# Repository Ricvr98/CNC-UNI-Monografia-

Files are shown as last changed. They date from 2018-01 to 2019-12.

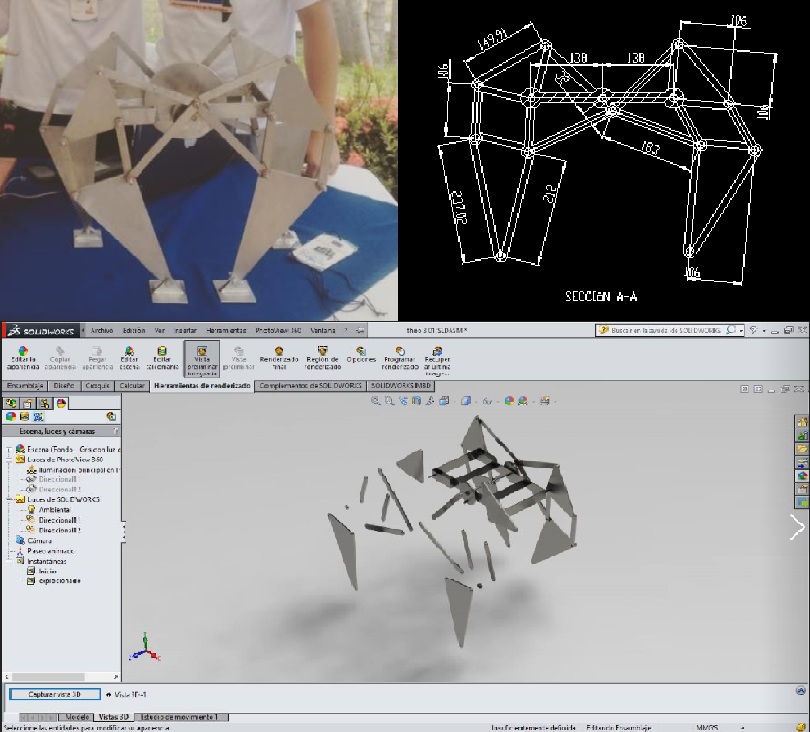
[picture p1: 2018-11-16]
conferencia/imagenes/diseño.jpg

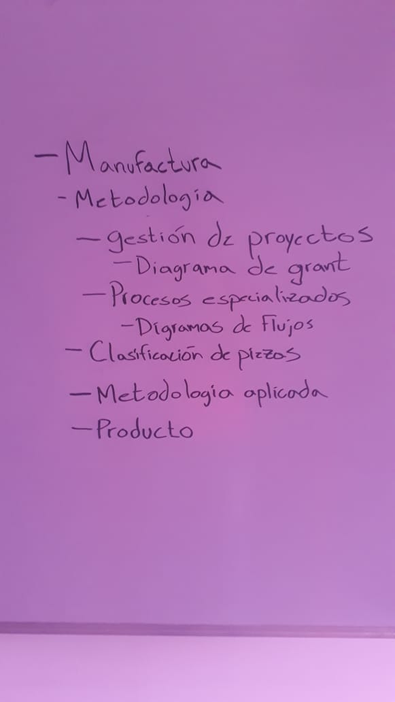
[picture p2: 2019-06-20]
bibliografia/Estructura manufactura.jpeg

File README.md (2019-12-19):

# CNC-UNI-Monografia-

-----------------CNC UNI 1.0------------------
===========================================================================================
Las máquinas de control numérico o CNC son el alma de la manufactura a gran escala
por lo tanto se ha decidido hacer un esfuerzo en entender la tecnología con el fin 
de facilitar la comprensión de cómo y cuándo se deben utilizar, además de que planteamos 
una metodología de diseño mecánico la cual hemos ido refinando a lo largo de los proyectos 
en los que hemos trabajado dejando en esta investigación nuestras conclusiones de cómo se 
debe elaborar un producto en este caso un CNC siendo esta monografía un arma de doble filo 
en donde se plantean los medios(Manufactura en máquinas CNC) para llevar a cabo el fin
(Producto) que se proponga. No está de más decir que se ha tratado de utilizar lo último 
en tendencias de diseño y que nuestro proyecto es open hardware el cual tiene como objetivo 
beneficiar a la mayor cantidad de gente directa o indirectamente.
___________________________________________________________________________________________
Importante
___________________________________________________________________________________________
Todo el software compartido en este proyecto es de terceros esto significa que ninguno de
estos programas fue desarrollodo por nosotros. Este proyecto mas bien plantea una recopilacion
de los programas que a nuestro criterio recomendamos.

La maquina necesita un conjunto de componentes electronicos y sus correspondientes software
para funcionar correctamente.
-------------------------------------------------------------------------------------------
Arduino MEGA 2560 + Ramps 1.4
-------------------------------------------------------------------------------------------
Este conjunto distribuye las instruciones de movimiento a los motores de los correspondientes
ejes.
El software relevante para el funcionamiento de este conjunto es:
	-IDE arduino
	-Librerias Marlin CNC y U8glib (https://github.com/MarlinFirmware/Marlin)
--------------------------------------------------------------------------------------------
Cad-cam 
--------------------------------------------------------------------------------------------
Con el objetivo de generar las geometrias de manera apropiada para esto proponemos el uso de 
Fusion 360 sin embargo se necesita el postprocesodor correcto para que la maquina entienda 
las instrucciones correctamente por lo tanto como postprocesador proponemos.
	-MPCnc Postprocessor (https://github.com/martindb/mpcnc_posts_processor)
---------------------------------------------------------------------------------------------
Interprete
---------------------------------------------------------------------------------------------
El trabajo del interprete es comunicar al microcontorlador de la maquina las instrucciones
previamente generadas en el programa CAM de una manera ordenada y legible para la maquina,
para esta tarea proponemos como interprete:
-Cncjs (https://github.com/cncjs/cncjs)

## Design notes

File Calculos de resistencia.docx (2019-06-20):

A continuación, se presentarán los cálculos de los ejes correspondientes para calcular la deflexión que se produce en la estructura metálica de la máquina. El método que se empleara para el cálculo de la deflexión máxima es el de área-momento.

Se hizo el análisis del cabezal del eje Z para el cual se hicieron algunas idealizaciones, tomando en cuenta que la fuerza que se aplica en el cabezal para transmitirla a las guías del eje Y es la componente de la fuerza de corte en el eje X, por lo tanto, se obtiene el siguiente análisis:

Material Aluminio

Perfil en L

E=69 GP_a

I_X =I_Y =1.44x10^5 mm^4

∑ F_X =0

∑ F_Y =0

∑ M_A =0

R_(Ax) +R_(Bx) -F_1 =0

R_(Ay) +R_(By) =0

(R_(Bx) *L_(AB) )+(F_1 *L_(AC) )=0

R_(Ax) =-R_(Bx) +F_1

R_(Ay) =-R_(By)

R_(Bx) =(F_1 *L_(AC))/(L_(AB))

R_(Bx) =(131.44N*157.3mm)/(60.3mm)

R_(Bx) =343.0529N

R_(Ax) =-342.8775N+131.44N

R_(Ax) =-211.6129N

Cálculo del área-momento

B=(M_B)/(EI)

B=(-12749.68N)/((69*10^3 N*mm^2 )(1.44*10^5 mm^4 ))

B=-1.2832*10^(-6) mm^(-1)

∆_c =|t_(C/A) |-∆^(´)

Por relación de triángulos semejantes se tiene que:

(∆^(´))/(L_(AC))=(t_(B/A))/(L_(AB))

∆^(´) =(t_(B/A) *L_(AC))/(L_(AB))

∆^(´) =(157.3mm)/(60.3mm)*t_(B/A)

∆^(´) =2.61*t_(B/A)

|t_(B/A) |=1/3L_(AB) *(1/2*M/(EI)*L_(AB) )

|t_(B/A) |=1/3(60.3mm)(1/2*M/(EI)*60.3mm)

|t_(B/A) |=605.0104 mm^2 *M/(EI)

|t_(C/A) |=L_(AB) *(1/2*M/(EI)*L_(AC) )

|t_(C/A) |=60.3mm*(1/2*M/(EI)*157.3mm)

|t_(C/A) |=4737.1563mm^2 *M/(EI)

∆_c =|t_(C/A) |-∆^(´)

∆_c =|t_(C/A) |-2.61*t_(B/A)

∆_c =4737.1563 mm^2 *M/(EI)-2.61*(605.0104 mm^2 *M/(EI))

∆_c =(4737.1563 mm^2 *1.2832*10^(-6) mm^(-1) )-2.61*(605.0104 mm^2 *1.2832*10^(-6) mm^(-1) )

∆_c =4.0524*10^(-3) mm

Los rodamientos del cabezal del eje Z están distribuidos de forma simétrica, por lo tanto, se tiene la deflexión máxima calculada para el cabezal es igual en ambos lados de los cojinetes. De esta manera se tiene que esta deflexión máxima es permisible a la hora de maquinar sobre aluminio.

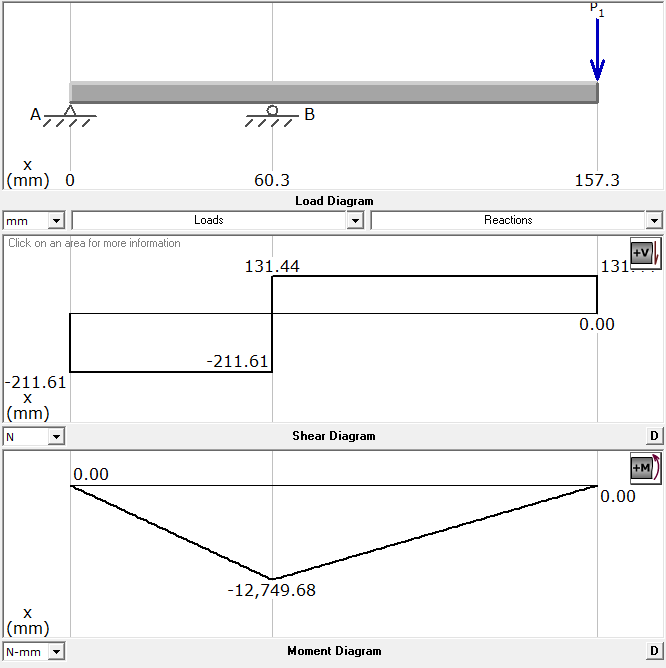
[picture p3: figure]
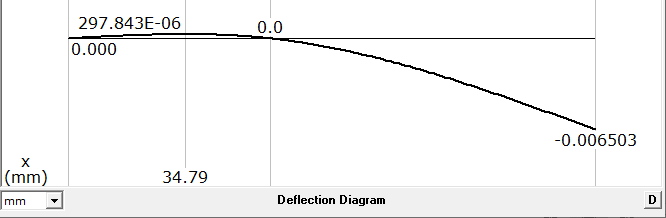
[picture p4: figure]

Guías lineales

Material: Aleación Cromo-Níquel

Perfil Circular

E=210 GP_a ≅210 (KN)/(mm^2)

I=1.02x10^3 mm^4

En el análisis de las fuerzas que actúan en las guías lineales se observa que esta doblemente empotrada y es de condición hiperestática. Se observo en el libro de resistencia de materiales 5ta edición de Robert L. Mott en el apéndice A-25 que la guía se comporta de la misma manera en que está representado ahí, por lo que se ocuparan las formulas ya planteadas solo cambiando el signo de la formula según el sentido de la fuerza.

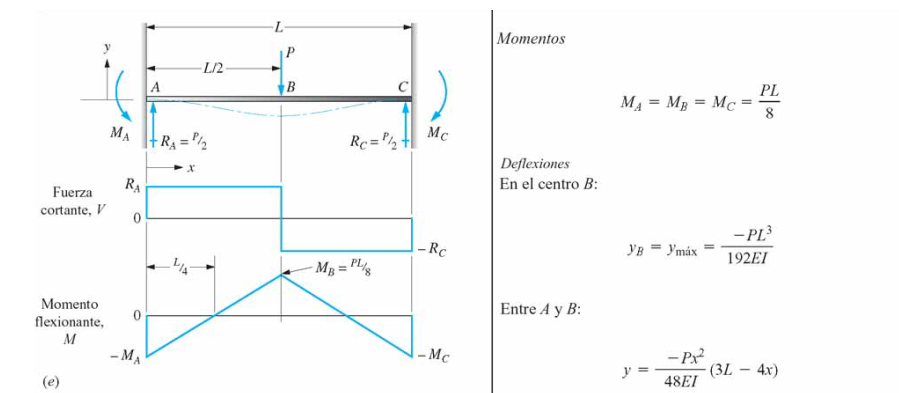
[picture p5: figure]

Para la Guía Lineal #1 la fuerza se comporta en el mismo sentido de la figura.

Las reacciones están de la siguiente manera:

R_A =R_B =(F_1)/2

R_A =(211.6129 N)/2

R_A =105.80645 N

Los momentos flexionantes son:

M_A =M_B =M_C =(F_1 L)/8

M_A =(211.80645 N*274 mm)/8

M_A =7247.7018 N*mm

La deflexión máxima en el punto B es:

y_B =y_(máx) =(F_1 *L_(AC)^3)/(192EI)

y_B =(211.80645N*(274mm)^3)/(192*(210*10^3 N/(mm^2))*(1.02*10^3 mm^4 ))

y_B =0.10581 mm

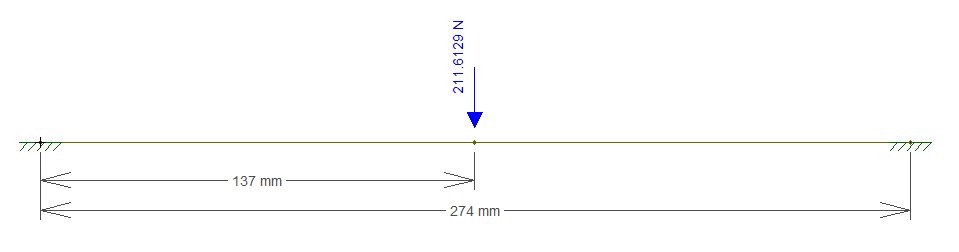
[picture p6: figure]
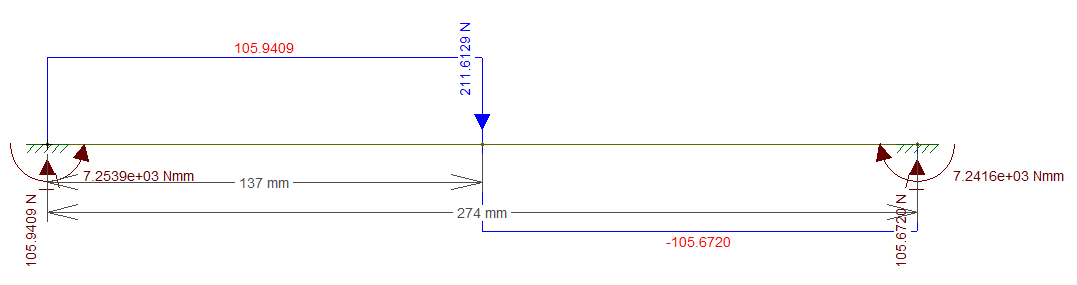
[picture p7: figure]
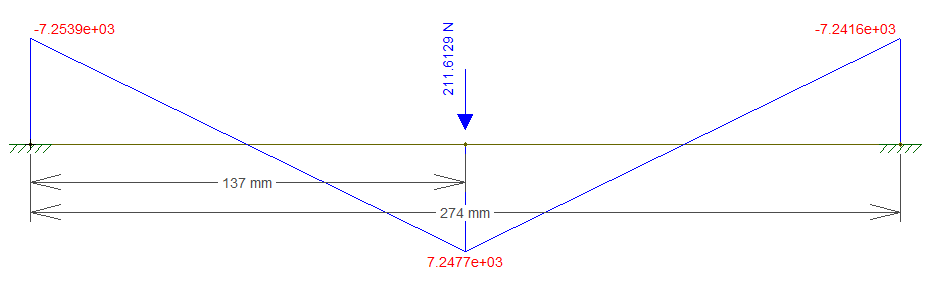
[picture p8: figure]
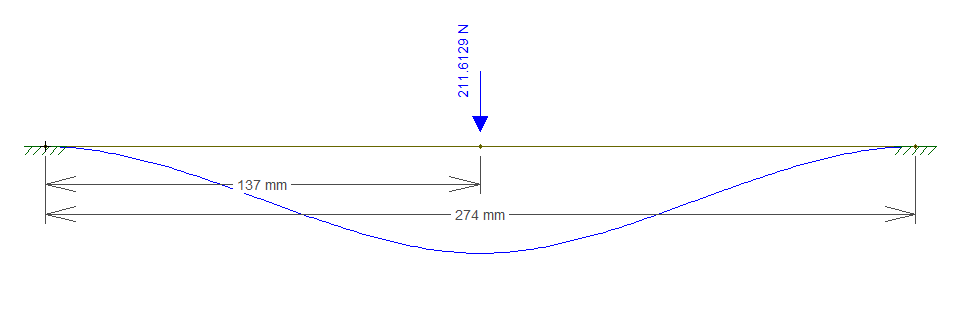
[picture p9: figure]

0.1058 mm

La guía lineal #2 se comporta de la misma manera solo que el sentido de la fuerza es en sentido contrario.

Las reacciones están de la siguiente manera:

R_A =R_B =(F_1)/2

R_A =(343.0529 N)/2

R_A =171.52645 N

Los momentos flexionantes son:

M_A =M_B =M_C =(F_1 L)/8

M_A =(343.0529 N*274 mm)/8

M_A =11749.56183 N*mm

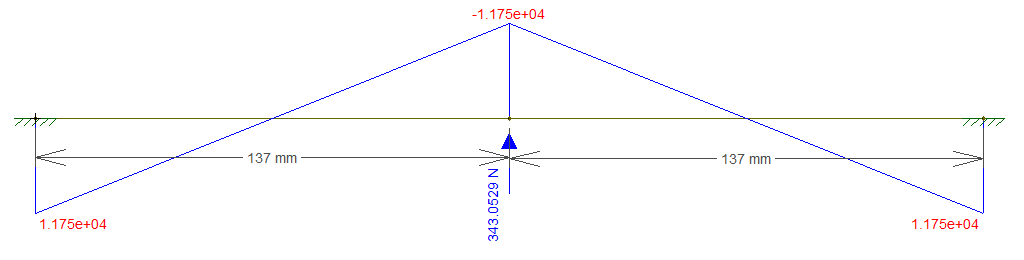
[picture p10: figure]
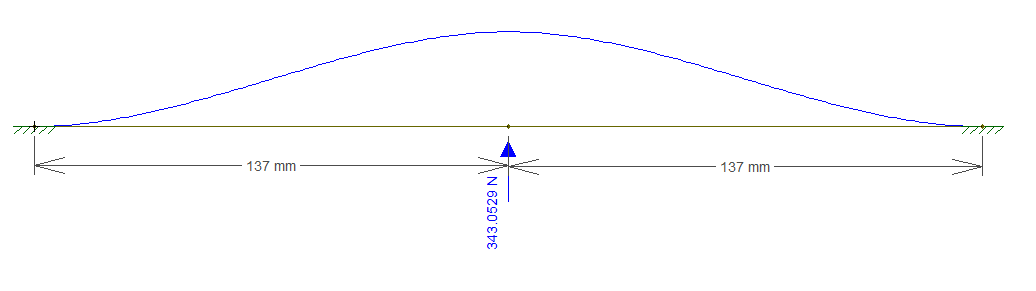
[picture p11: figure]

La deflexión máxima en el punto B es:

0.1716 mm

y_B =y_(máx) =(F_1 *L_(AC)^3)/(192EI)

y_B =(343.0529N*(274mm)^3)/(192*(210*10^3 N/(mm^2))*(1.02*10^3 mm^4 ))

y_B =0.1716 mm

Cálculo de resistencia de los parales de la estructura metálica

Material: Acero estructural

E=200 GP_a =200 (KN)/(mm^2)

∑ F_X =0

∑ F_z =0

∑ M_A =0

R_(Ax) -F_2 +F_1 =0

R_(Az) =0

M_A +M_B -M_C +(F_2 *L_(AB) )-(F_1 *L_(AC) )=0

R_(Ax) =F_2 -F_1

R_(Ax) =171.52645N-105.80645N

R_(Ax) =65.72N

M_A =-M_B +M_C +(F_2 *L_(AB) )-(F_1 *L_(AC) )

M_A =-11749.56183N*mm+7247.7418+(171.52645N*292.5mm)-(105.80645N*470mm)

M_A =-11749.56183N*mm+7247.7418+(50171.48663N*mm)-(49729.0315N*mm)

M_A =-4059.3649N*mm

Es un perfil rectangular hueco de 2”x1”x1/16” de medidas externas (50.8mm x 25.4mm x 1.5875mm)

Medidas internas 1.875”x0.875” (47.625mm x 22.225mm)

I=(b*h^3)/12-(b*h^3)/12

I=((25.4mm)*(50.8mm)^3)/12-((22.225mm)(47.625mm)^3)/12

I=277487.6171mm^4 -200062.407mm^4

I=77.43x10^3 mm^4

Cálculo del área-momento

A=(M_A)/(EI)

A=(4059.36491N*mm)/((2.00*10^5 N*mm^2 )(77.43*10^3 mm^4 ))

B=2.6*10^(-7) mm^(-1)

B=(M_B)/(EI)

B=(23282.46491N*mm)/((2.00*10^5 N*mm^2 )(77.43*10^3 mm^4 ))

B=1.5*10^(-6) mm^(-1)

B=(M_B)/(EI)

C=(11532.90308N*mm)/((2.00*10^5 N*mm^2 )(77.43*10^3 mm^4 ))

C=7.5*10^(-7) mm^(-1)

C=(M_A)/(EI)

C=(-7247.7418N*mm)/((2.00*10^5 N*mm^2 )(77.43*10^3 mm^4 ))

C=-4.7*10^(-7) mm^(-1)

∆_c =|t_(B/A) |+∆^(´)

Por relación de triángulos semejantes se tiene que:

(∆^(´))/(L_(AC))=(t_(B/A))/(L_(AB))

∆^(´) =(t_(B/A) *L_(AC))/(L_(AB))

∆^(´) =(470mm)/(292.5mm)*t_(B/A)

∆^(´) =1.61*t_(B/A)

|t_(B/A) |=1/3L_(AB) *(1/2*(M_1)/(EI)*L_(AB) )+1/2L_(AB) *((M_2)/(EI)*L_(AB) )

|t_(B/A) |=1/3(292.5mm)*(1/2*1.2*10^(-6) mm^(-1) *292.5mm)+1/2*292.5mm*(2.6*10^(-7) mm^(-1) *292.5mm)

|t_(B/A) |=0.02mm+0.01mm

|t_(B/A) |=0.03mm (Deflexión máxima en el punto B)

∆^(´) =1.61*t_(B/A)

∆^(´) =1.61*0.03

∆^(´) =0.05mm

∆_c =|t_(B/A) |+∆^(´)

∆_c =0.03mm+0.05mm

∆_c =0.08mm(Deflexión máxima en el punto C)

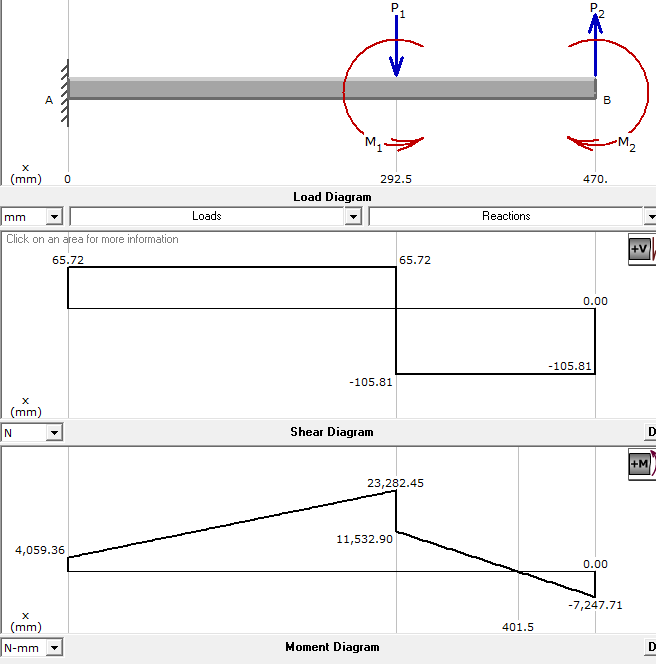
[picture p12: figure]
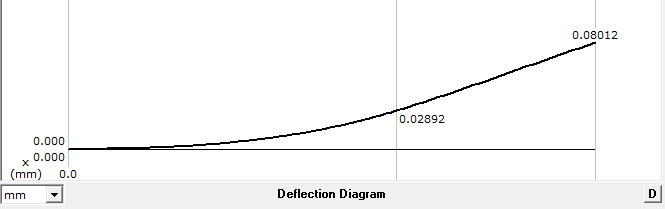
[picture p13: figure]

Los parales verticales de la estructura metálica tienen una deflexión máxima de 0.08 mm, por lo tanto, se concluye que la estructura metálica es lo suficientemente rígida para soportar el maquinado de materiales como el aluminio.

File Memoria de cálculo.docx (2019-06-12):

Memoria de cálculo.

Nota: se tomará el área como unidad correspondiendo a la unidad de medida de la fuerza de corte.

Fc1= 500 N/mm (fuerza de corte especifica por unidad de mm)

Ac = 1 mm (Área de Corte)

ae= 5mm (profundidad de corte radial)

Z’= 0.15 (factor de corrección)

Z= 4 (número de filos)

n= RPM (revoluciones por minuto)

Vf= 1000 mm/min (velocidad de avance)

f_z =(V_f)/(n*z) (avance por diente)

f_z =(1000 (mm)/(min))/((12000 rpm*4))

f_z =0.02083 (mm)/(rev)

h_m =(f_z *a_e *360)/(D*π*cos^(-1) [1-(2a_e)/D])

h_m =(0.02083(mm)/(rev)*5mm*360)/(9mm*π*cos^(-1) [1-(2*5mm)/(9mm)])

h_m =0.01376 mm

F_c^(,) =F_(C_1) *h_m ^(z^(,)) (fuerza de corte especifica)

F_c^(,) =500 N/(mm) *(0.01376mm)^0.15

F_c^(,) = 262.88 N/(mm^2)

F_c =F_c^(,) *A_c (Fuerza de corte)

F_c =262.88 N/(mm^2)*1 mm^2

F_c =262.88 N

# Tornillo de potencia del eje Z

-Z

Z

## Movimiento vertical

Fuerzas que actúan.

Fi= 4.90 kgf

Ff= 0.882 kgf

N= 4.90 kgf

µ=0.18

Fm= 262.88 N ≈ 26.7971 kgf

Velocidades de trabajo.

Vo= 0

V1= Vmáx

V2= Vmáx

V3= Vm

V4= Vm

V5= 0

V6= Vm

V7= Vm

V8= Vmáx

V9= Vmáx

V10= 0

Ff

Fuerzas que actúan en el tornillo dependiendo de las velocidades de trabajo.

Fi

Fa_1 =F_i -F_f ; Fa_1 =(4.9-0.882)kgf ; Fa_1 =4.018 kgf

Ff

Fa_2 =-F_f ; Fa_2 =-0.882 kgf

Ff

Fi

Fa_3 =F_i -F_f ; Fa_3 =(4.9-0.882)kgf ; Fa_3 =4.018 kgf

Fm

Fa_4 =F_f -F_m ; Fa_4 =(0.882-26.7971)kgf ; Fa_4 =-25.9151 kgf

Ff

Ff

Fa_5 =F_f ; Fa_5 =0.882 kgf

Ff

Fa_6 =-F_f ; Fa_6 =-0.882 kgf

Ff

Fa_7 =F_m -F_f ; Fa_7 =(26.7971-0.882)kgf ; Fa_7 =25.9151 kgf

Fm

Ff

Fi

Fa_8 =F_f -F_i ; Fa_8 =(0.882-4.9)kgf ; Fa_8 =-4.018

Ff

Fa_9 =F_f ; Fa_9 =0.882 kgf

Ff

Fi

Fa_10 =F_f -F_i ; Fa_10 =(0.882-4.9)kgf ; Fa_10 =-4.018 kgf

Torque requerido para subir una carga.

F= 4.9 kgf

f=0.18

φ= 14.5°

D= 7.9375 mm

P= 1.81356 mm (L)

Dr=5.4356 mm

Dp= 6.63956 mm

At= 28.6322008 plg²

As=280.257504 plg²

tanλ=L/(πD_p) (ángulo de avance)

tanλ=(1.81356mm)/(π*6.63956mm) ; λ=tan^(-1) ((1.81356mm)/(π*6.63956mm))

λ=4.9691°

Torque necesario para subir una carga.

T_u =(FD_p)/2[(cosϕtanλ+f)/(cosϕ-ftanλ)]

T_u =(4.90kgf*6.63956mm)/2[(cos(14.5)tan(4.9691)+0.18)/(cos(14.5)-0.18tan(4.9691))]

T_u =4.5116 kgf*mm

T_u =(4.5116 kgf*mm)*(1cm)/(10mm)*(9.81N)/(1kgf)

T_u =4.4259 N*cm

Torque requerido para bajar una carga.

T_d =(FD_p)/2[(f-cosϕtanλ)/(cosϕ+ftanλ)] Torque necesario para bajar una carga

T_d =(4.90kgf*6.63956mm)/2[(0.18-cos(14.5)tan(4.9691))/(cos(14.5)+0.18tan(4.9691))]

T_d =1.5844 kgf*mm

T_d =(1.5844 kgf*mm)*(1cm)/(10mm)*(9.81N)/(1kgf)

T_d =1.5543 N*cm

Tornillo de potencia del eje X

## Movimiento horizontal

X

-X

Fuerzas que actúan.

Fi= 7.02 kgf

Ff= 1.2636 kgf

N= 7.02 kgf

µ=0.18

Fm=262.88 N ≈ 26.7971 kgf

Velocidades de trabajo.

Vo= 0

V1= Vmáx

V2= Vmáx

V3= Vm

V4= Vm

V5= 0

V6= Vm

V7= Vm

V8= Vmáx

V9= Vmáx

V10= 0

Fi

-Ff

Fuerzas que actúan en el tornillo dependiendo de las velocidades de trabajo.

Fa_1 =F_i -F_f ; Fa_1 =(7.02-1.2636)kgf ; Fa_1 =5.7564 kgf

-Ff

Fi

-Ff

Fa_2 =-F_f ; Fa_2 =-1.2636 kgf

Fa_3 =F_i -F_f ; Fa_3 =(7.02-1.2636)kgf ; Fa_3 =5.7564 kgf

Fa_4 =F_f -F_m ; Fa_4 =(1.2636-26.7971)kgf ; Fa_4 =-25.5335 kgf

Ff

-Fm

Ff

Fa_5 =F_f ; Fa_5 =1.2636 kgf

-Ff

-Ff

Fa_6 =-F_f ; Fa_6 =-1.2636 kgf

Fm

Fa_7 =F_m -F_f ; Fa_7 =(26.7971-1.2636)kgf ; Fa_7 =25.5335 kgf

Fa_8 =F_f -F_i ; Fa_8 =(1.2636-7.02)kgf ; Fa_8 =-5.7564 kgf

Ff

-Fi

Ff

Fa_9 =F_f ; Fa_9 =1.2636 kgf

Ff

-Fi

Fa_10 =F_f -F_i ; Fa_10 =(1.2636-7.02)kgf ; Fa_10 =-5.7564 kgf

Torque necesario para subir una carga.

T_u =(FD_p)/2[(cosϕtanλ+f)/(cosϕ-ftanλ)]

T_u =(7.02kgf*6.63956mm)/2[(cos(14.5)tan(4.9691)+0.18)/(cos(14.5)-0.18tan(4.9691))]

T_u =6.4636 kgf*mm

T_u =(6.4636 kgf*mm)*(1cm)/(10mm)*(9.81N)/(1kgf)

T_u =6.3408 N*cm

Torque requerido para bajar una carga.

T_d =(FD_p)/2[(f-cosϕtanλ)/(cosϕ+ftanλ)] Torque necesario para bajar una carga

T_d =(7.02kgf*6.63956mm)/2[(0.18-cos(14.5)tan(4.9691))/(cos(14.5)+0.18tan(4.9691))]

T_d =2.2700 kgf*mm

T_d =(2.2700 kgf*mm)*(1cm)/(10mm)*(9.81N)/(1kgf)

T_d =2.2269 N*cm

# Tornillo de potencia del eje Y

## Movimiento horizontal

Y

-Y

Fuerzas que actúan.

Fi= 3.09 kgf

Ff= 0.5562 kgf

N= 3.09 kgf

µ=0.18

Fm=262.88 N ≈ 26.7971 kgf

Velocidades de trabajo.

Vo= 0

V1= Vmáx

V2= Vmáx

V3= Vm

V4= Vm

V5= 0

V6= Vm

V7= Vm

V8= Vmáx

V9= Vmáx

V10= 0

Fi

-Ff

Fuerzas que actúan en el tornillo dependiendo de las velocidades de trabajo.

Fa_1 =F_i -F_f ; Fa_1 =(3.09-0.5562)kgf ; Fa_1 =2.5338 kgf

-Ff

Fi

-Ff

Fa_2 =-F_f ; Fa_2 =-0.5562 kgf

Fa_3 =F_i -F_f ; Fa_3 =(3.09-0.5562)kgf ; Fa_3 =2.5338 kgf

Fa_4 =F_f -F_m ; Fa_4 =(0.5562-26.7971)kgf ; Fa_4 =-26.2409 kgf

Ff

-Fm

Ff

Fa_5 =F_f ; Fa_5 =0.5562 kgf

-Ff

-Ff

Fa_6 =-F_f ; Fa_6 =-0.5562 kgf

Fm

Fa_7 =F_m -F_f ; Fa_7 =(26.7971-0.5562)kgf ; Fa_7 =26.2409 kgf

Fa_8 =F_f -F_i ; Fa_8 =(0.5562-3.09)kgf ; Fa_8 =-2.5338 kgf

Ff

-Fi

Ff

Fa_9 =F_f ; Fa_9 =0.5562 kgf

Ff

-Fi

Fa_10 =F_f -F_i ; Fa_10 =(0.5562-3.09)kgf ; Fa_10 =-2.5338 kgf

Torque necesario para subir una carga.

T_u =(FD_p)/2[(cosϕtanλ+f)/(cosϕ-ftanλ)]

T_u =(3.09kgf*6.63956mm)/2[(cos(14.5)tan(4.9691)+0.18)/(cos(14.5)-0.18tan(4.9691))]

T_u =2.8451 kgf*mm

T_u =(2.8451 kgf*mm)*(1cm)/(10mm)*(9.81N)/(1kgf)

T_u =2.7910 N*cm

Torque requerido para bajar una carga.

T_d =(FD_p)/2[(f-cosϕtanλ)/(cosϕ+ftanλ)] Torque necesario para bajar una carga

T_d =(3.09kgf*6.63956mm)/2[(0.18-cos(14.5)tan(4.9691))/(cos(14.5)+0.18tan(4.9691))]

T_d =0.9992 kgf*mm

T_d =(0.9992 kgf*mm)*(1cm)/(10mm)*(9.81N)/(1kgf)

T_d =0.9802 N*cm

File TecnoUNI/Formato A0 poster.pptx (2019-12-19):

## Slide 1

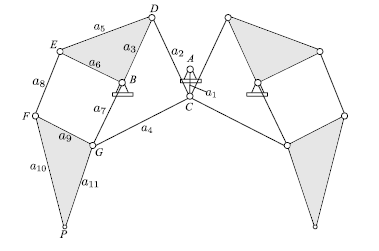
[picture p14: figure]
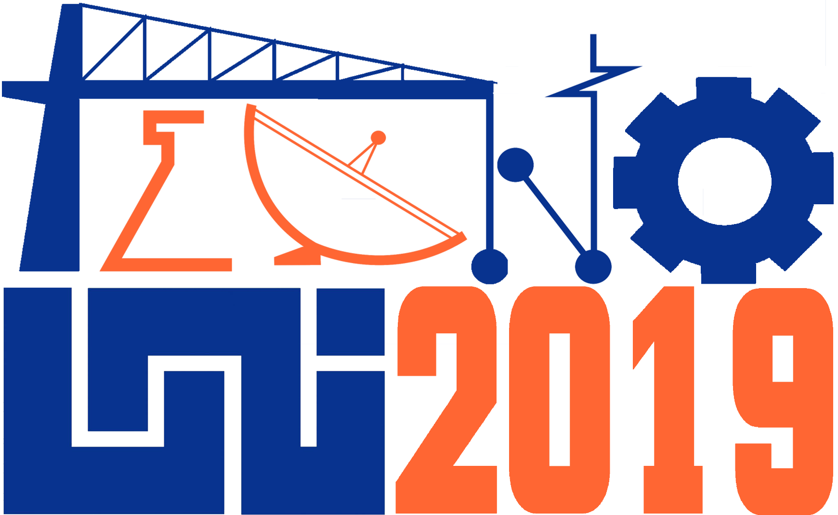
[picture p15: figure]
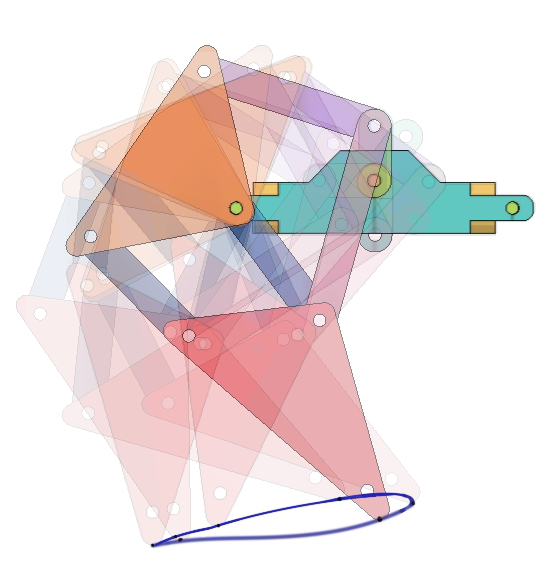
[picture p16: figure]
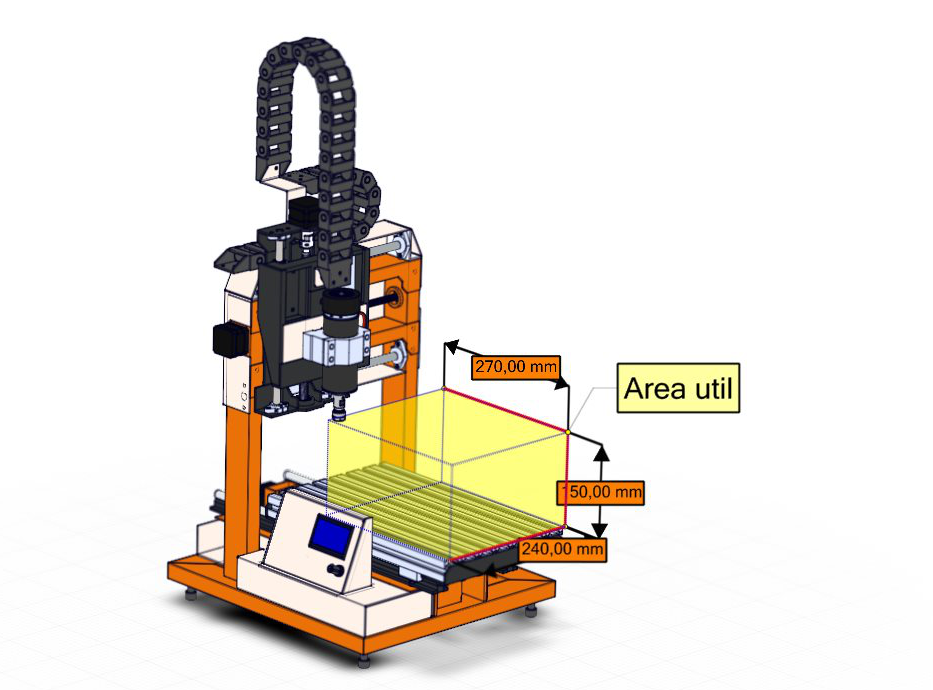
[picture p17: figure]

Manufactura en maquinaria CNC aplicada a
proyectos académicos y posibles usos en la
industria local

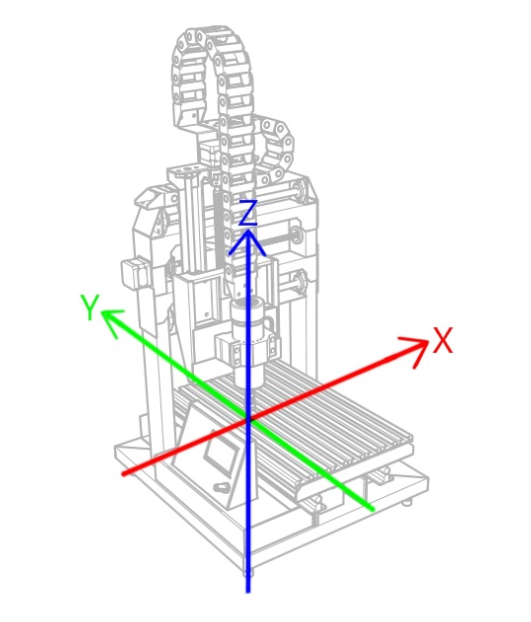
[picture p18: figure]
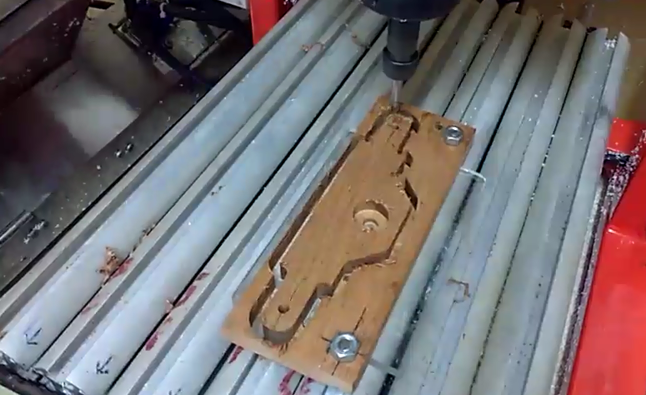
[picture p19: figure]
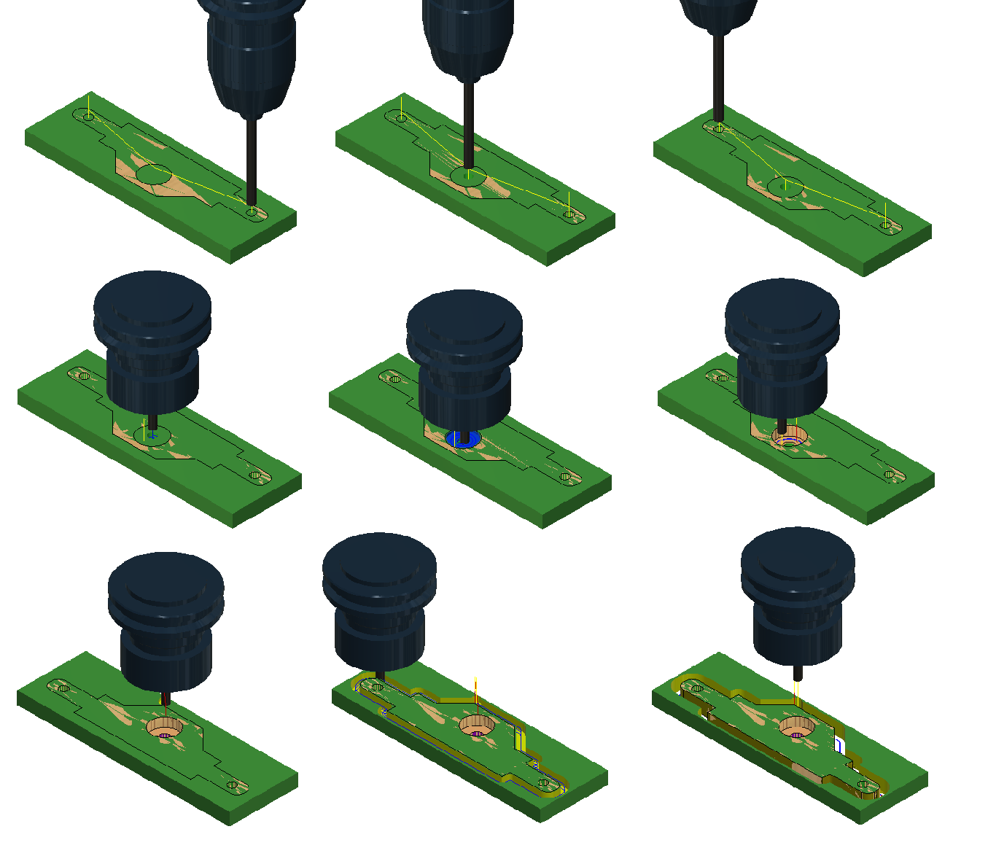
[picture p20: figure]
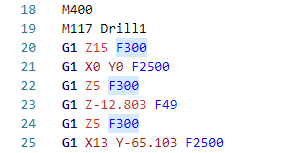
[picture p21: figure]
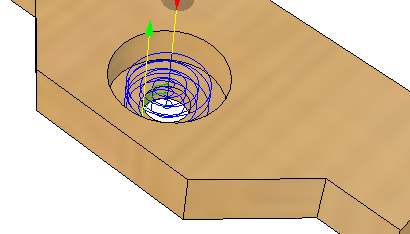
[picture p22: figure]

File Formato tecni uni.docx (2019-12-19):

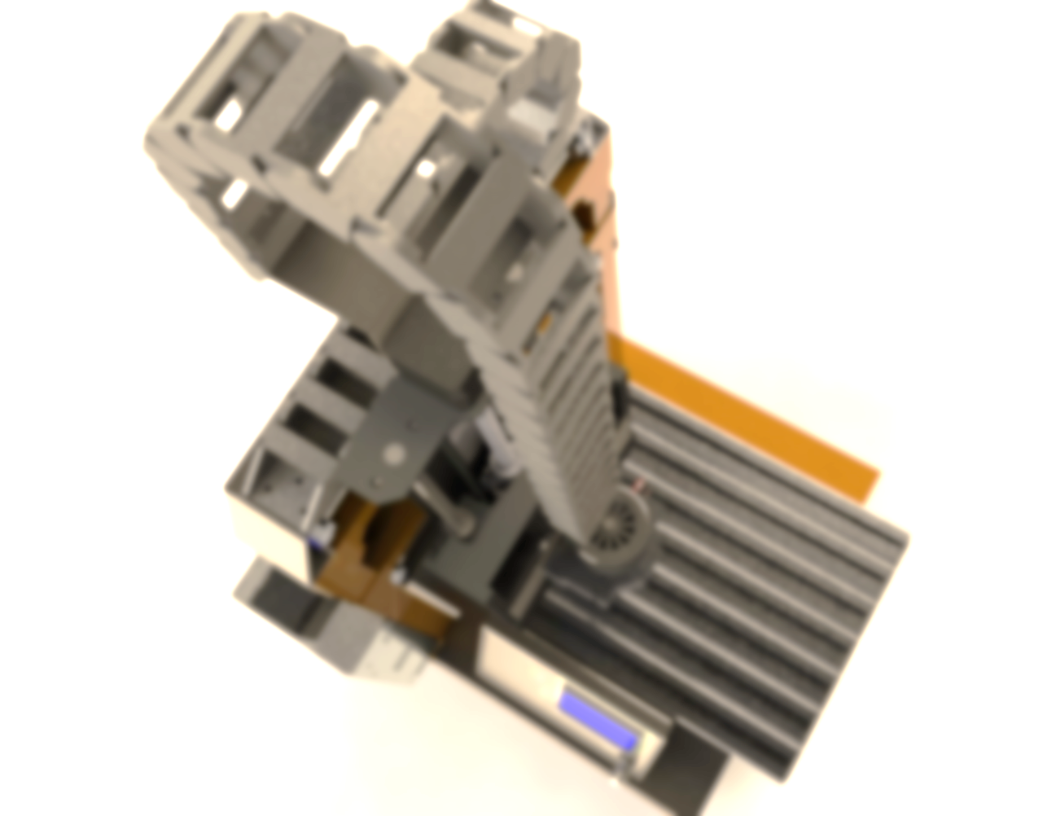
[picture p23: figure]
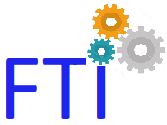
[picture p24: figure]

Convocatoria 2019

Para el Desarrollo de Propuestas Estudiantiles de Investigación, Desarrollo e Innovación (I+D+i) con Base en Necesidades y Demandas.

[Soportada en el Reglamento de Becas para el Fomento de Proyectos Estudiantiles de I+D+i de la UNI]

PROPUESTA ESTUDIANTIL DE INVESTIGACIÓN, DESARROLLO E INNOVACIÓN (I+D+i) CON BASE EN NECESIDADES Y DEMANDAS

Título:

Manufactura en maquinaria CNC aplicada a proyectos académicos y posibles usos en la industria local

Tutor:

Ing. Mary Triny Gutiérrez Mendoza

Autores:

Ariel Enoc Cisnero Rizo

Richard José Valverde Ramírez

Carrera(s) y Facultad(es):

Ingeniería mecánica

Facultad de Tecnologías de la Industrias (FTI)

Managua, 21 del 2019

Tabla de Contenido

# 1. RESUMEN DEL PROYECTO

Las máquinas de control numérico o CNC son el alma de la manufactura a gran escala por lo tanto decidimos hacer un esfuerzo en entender la tecnología con el fin de facilitar la comprensión de cómo y cuándo se deben utilizar, además de que planteamos una metodología de diseño mecánico la cual hemos ido refinando a lo largo de los proyectos en los que hemos trabajado dejando en esta investigación nuestras conclusiones de cómo se debe elaborar un producto siendo esta investigación un arma de doble filo en donde se plantean los medios(Manufactura en máquinas CNC) para llevar a cabo el fin(Producto) que se proponga además se ha tratado de utilizar lo último en tendencias de diseño y que nuestro proyecto es open hardware el cual tiene como objetivo beneficiar a la mayor cantidad de gente directa o indirectamente.

En el transcurso de este proyecto se utilizó una maquina (CNC router de tres ejes) desarrollada como monografía por los autores de esta investigación para llevar a cabo un proyecto (mecanismo Theo Jansen) el cual consiste en la fabricación de los componentes de esta máquina con la ventaja de que dicho mecanismo (Theo jansen) ya se había fabricado de manera artesanal anteriormente por nosotros mismos permitiéndonos así comparar los métodos de manufactura utilizados en los respectivos prototipos (artesanal/automatizado) con el objetivo de argumentar sobre las ventajas que presentan los CNC’s como proceso de manufactura y en qué circunstancias su uso es adecuado, no está de más decir que el campo de aplicación de esta investigación abarca tanto el académico como el industrial/comercial.

# 2. IDENTIFICACIÓN DEL PROBLEMA Y JUSTIFICACIÓN

Personalmente la maquina la fabricamos debido a las dificultades que pasamos al fabricar otros proyectos anteriormente, así que decidimos diseñar y fabricar nuestra propia herramienta; en el camino logramos observar que este tipo de máquinas tienen una gran utilidad la cual se acentúa en un país como lo es Nicaragua principalmente porque la mayoría de lo que se exporta son materias primas y hacemos énfasis en esto debido a que una mayor presencia de los ingenieros en el campo de la manufactura aumentaría el dinero percibido por el país ya que los procesos de manufactura como los ofrecidos por los sistemas CNC’s aportan valor a los productos que se exporten. En corto plazo el objetivo del proyecto es ofrecer a la Facultad de Tecnologías de la Industria (FTI) una nueva herramienta con la cual hacer nuevos proyectos además de una metodología probada sobre cómo llevarlos a cabo; a largo plazo es sensibilizar a la comunidad en general de las ventajas que presenta la incorporación de la maquinaria CNC a los procesos artesanales con el fin de aumentar la calidad y el volumen de los productos procesados localmente.

# 3. OBJETIVOS

## 3.1. Objetivo General

Demostrar cómo se debe utilizar la herramienta propuesta (CNC router de tres ejes) mediante un proyecto desarrollado con la misma.

## 3.2. Objetivos Específicos

- Fabricar una maquina a partir de un diseño propuesto con el fin de ejemplificar cuales son los pasos a seguir al emplear maquinaria CNC (Router CNC de tres ejes).
- Demostrar las ventajas de este tipo de máquinas en la industria local.
- Justificar ante las autoridades universitarias correspondiente un cambio en el pensum en pro de la mejora de las habilidades que se desarrollan en la carrera de ingeniería mecánica acorde a la metodología de manufactura expuesta.

# 4. RESULTADOS/PRODUCTOS/IMPACTOS ESPERADOS DEL PROYECTO

Actualmente a raíz del proyecto investigativo y monografía (CNC router de tres ejes) se ha dotado a la universidad de la herramienta adecuada para desarrollar las habilidades de los estudiantes de la comunidad universitaria en proyectos de mayor complejidad., es decir parte de los resultados que se buscan es demostrar las capacidades de este tipo de maquina (Maquinas CNC en general) cuando se usan con la metodología adecuada en proyectos multidisciplinarios.

Con el objetivo de verificar las mejoras en los procesos de manufactura se espera comparar dimensionalmente las piezas realizadas y obtener pruebas experimentales que avalen nuestros objetivos.

Acorde a los resultados de las pruebas se definirán los tipos de productos locales que podrían tener una mejora sustancial en términos de calidad y rentabilidad.

# 5. BENEFICIARIOS

Inicialmente el conjunto de máquina y metodología plantea ser un proyecto demostrativo con el único y simple objetivo de incentivar a la comunidad universitaria a generar propuestas de soluciones a problemas en la manera de productos. Principalmente la metodología de manufactura está enfocada al perfil de la ingeniería mecánica, pero hacemos énfasis que para un correcto funcionamiento es necesario crear equipos multidisciplinarios para generar una propuesta conjunta según el caso lo requiera.

Finalmente esperamos que como resultado estos proyectos mejoren de una u otra manera la calidad de vida de la población en general basándonos en que la generación de nuevos productos como solución de problemas le permite a la industria local ser más competitiva y a la vez la población en general pueda obtener mejores trabajos.

# 6. CRONOGRAMA

Objetivos Específicos | Actividades | Meses y Semanas
| | Mes 1 | | | | Mes 2 | | | | Mes 3 | | | | Mes 4
| | S1 | S2 | S3 | S4 | S1 | S2 | S3 | S4 | S1 | S2 | S3 | S4 | S1 | S2 | S3 | S4

# 7. PRESUPUESTO

Item | Descripción de bien y/o servicio | Unidad | Cantidad | Costo Unitario C$ | Costo Total C$
1 | Ejemplo: Arena motastepe | M3 | 2 | 173 | 346
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
Total | | | | | 7918

| Nombres | | Firmas
Coordinador del Proyecto
Vo. Bo. Tutor
Vo. Bo. Coordinador/a de Investigación

# 8. ANEXOS

[Ficha de ficha de identificación de demandas/necesidades o problemas que aparece en los Anexos del documento de la presente Convocatoria 2017-2018.

Se pueden incluir aquí los instrumento que se hayan diseñado para realizar el proyecto (e.g. ficha de levantamiento de campo, formato de encuesta, etc.]

MANUFACTURA EN MAQUINARIA CNC APLICADA A PROYECTOS ACADÉMICOS

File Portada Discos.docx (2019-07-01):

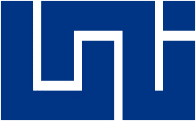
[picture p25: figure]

UNIVERSIDAD NACIONAL DE INGENIERIA

Facultad de Tecnología de la Industria

Ingeniería Mecánica

TITULO

Diseño y fabricación de una máquina Control Numérico Computarizado (CNC) ROUTER de 3 ejes para el taller de Máquinas Herramientas de la Facultad de Tecnología de la Industria en la Universidad Nacional de Ingeniería (UNI-RUPAP).

AUTORES

BR Ariel Enoc Cisnero Rizo

Br Richard José Valverde Ramírez

TUTOR

Ing Mary Triny Gutiérrez Mendoza

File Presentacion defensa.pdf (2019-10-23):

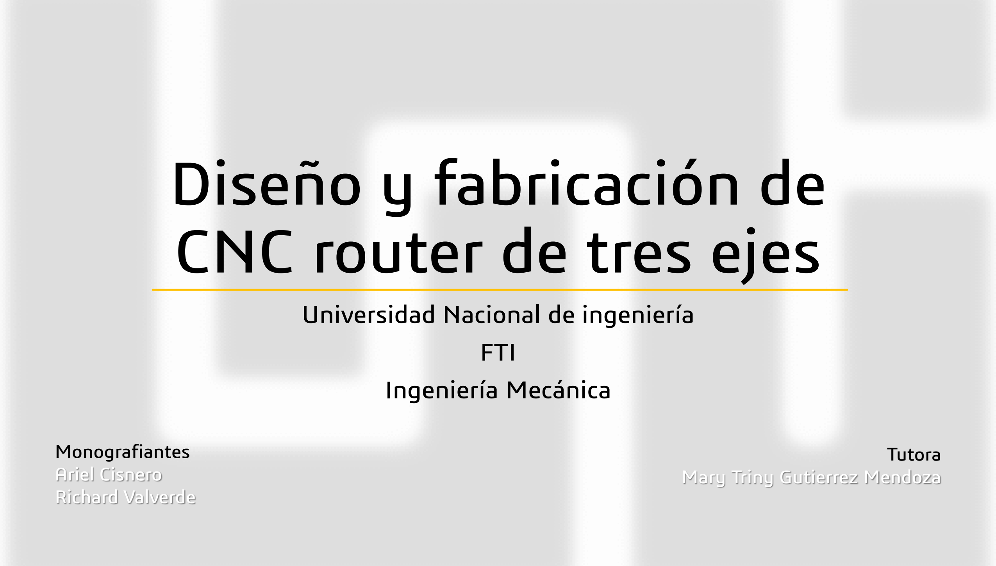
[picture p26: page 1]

# Diseño y fabricación de CNC router de tres ejes

Universidad Nacional de ingeniería FTI
Ingeniería Mecánica

Monografiantes
Ariel Cisnero
Richard Valverde

Tutora
Mary Triny Gutierrez Mendoza

## Objetivo Principal

Establecer los principios básicos de diseño de un router CNC garantizando la confiabilidad de los mecanismos utilizados en la máquina.

## Objetivos secundarios

- Plantear un diseño lo suficientemente robusto para lograr elaborar piezas de buena calidad.
- Definir el conjunto de piezas adecuadas dentro del diseño mecánico para que sea posible la fabricación del router CNC, tratando de mantener un balance entre fiabilidad y economía de manufactura.
- Fabricar la maquina (router CNC) lo más fielmente posible a los datos obtenidos en la fase de diseño.

## ¿Qué es un CNC?

- El control numérico computarizado es el uso de una computadora para controlar y monitorear los movimientos de una máquina herramienta•
- Todas las máquinas CNC comparten una característica en común tienen dos o más direcciones programables de movimiento llamadas ejes


## Diseño

Metodología

NO

Reconocimiento de
nuevas variables

Diseño de producto; Reconocimiento de la necesidad; ¿Cubre las necesidades del cliente?; Presentacion; Aislamiento de los factores que influyen en el problema; Propuesta de solución; Optimizacion; ¿Cumple los requisitos técnicos de diseño?

NO

“Se podría definir la actividad creativa como un tipo de proceso de aprendizaje en el que el profesor y el alumno se hallan en el mismo individuo.”

― Arthur Koestler
― Arthur Koestler

## Diseño

Definición del problema

Se diseñará una máquina (CNC) capaz de mecanizar plásticos y maderas en tres ejes con un volumen de maquinado de 25x25x15cm como el que se muestra en la imagen con una tolerancia de 0.5mm dentro del estándar de código G.


## Diseño

Mecánica


## Diseño

Electrónica


## Diseño

Optimización



## Diseño

Presentación

Mecánica; C$ 27.731,15 ; 44%; Electrónica; C$ 15.534,64; 25%; Mano de Obra; C$ 19.200,00; 31%; GASTOS FINACIEROS; Mecánica; Electrónica; Mano de Obra

## Aspectos financieros

Gasto total
Tipo de Gastos | Total C$ | Total $
Mecánica | C$ 27.731,15 | $843,86
Electrónica | C$ 15.534,64 | $507,19
Mano de Obra | C$ 19.200,00 | $581,82
Total | C$ 62.465,80 | $1.932,86

Manufactura | Planeación

“No se puede medir lo que no se ha planeado”


Manufactura | Ejecución


# PRIMERA VERSION

Manufactura | Ejecución


Manufactura | Ejecución


# VERSION 2.0

Manufactura | Ejecución


Manufactura | Ejecución


Manufactura | Ejecución


## Pruebas operativas


- El objetivo de este apartado verificar la precisión de la maquina mientras se
desarrolla un proyecto
demostrativo.
- Para optimizar el resultado el proyecto que se realizo ya había sido fabricado
anteriormente de manera
artesanal esto con el fin de comparar el rendimiento
entre procesos.

## Pruebas operativas


Diseño | Manufactura CNC

Pruebas operativas | Resultados


Columna1 | Cantidad de piezas | Proceso de manufactura | Tiempo(hrs) | Tolerancia promedio
V1 Mecanismo Theo jansen artesanal | 31 Manual | 272 | 0.65
V2 Mecanismo Theo jansen con CNC | 55 CNC | 64 | 0

Pruebas operativas | Resultados


## Conclusiones


- En esta ocasión la mejora de la máquina diseñada y fabricada tuvo el alcance deseado y por ende los objetivos planteados
para | esta | monografía | fueron | realizados | de | manera
satisfactoria.
- La hipótesis planteada al inicio del documento se demuestra porque la fabricación de la máquina proporcionará mejoras en la enseñanza de las diferentes asignaturas relacionadas a este tipo de máquinas, también ayudará a practicar si en un futuro se obtienen máquinas industrializadas de este tipo debido a que se basan en el mismo principio de funcionamiento.


# Fin

Gracias por su atención

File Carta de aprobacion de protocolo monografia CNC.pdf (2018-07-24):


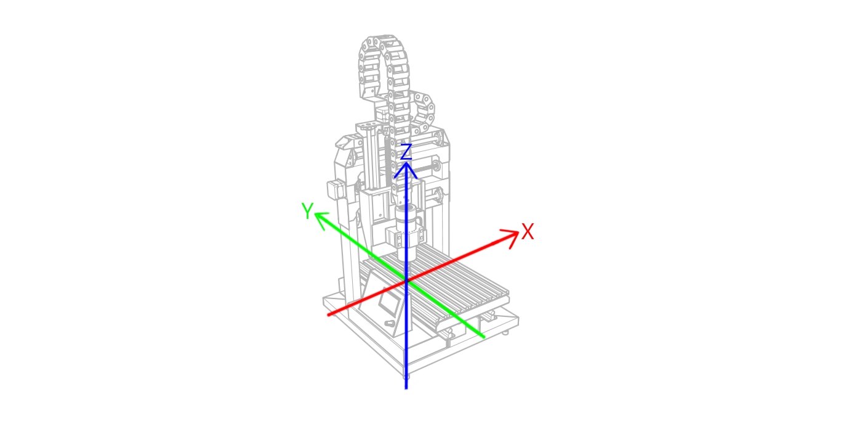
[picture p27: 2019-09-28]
renders/Ejes de referencia1.jpg

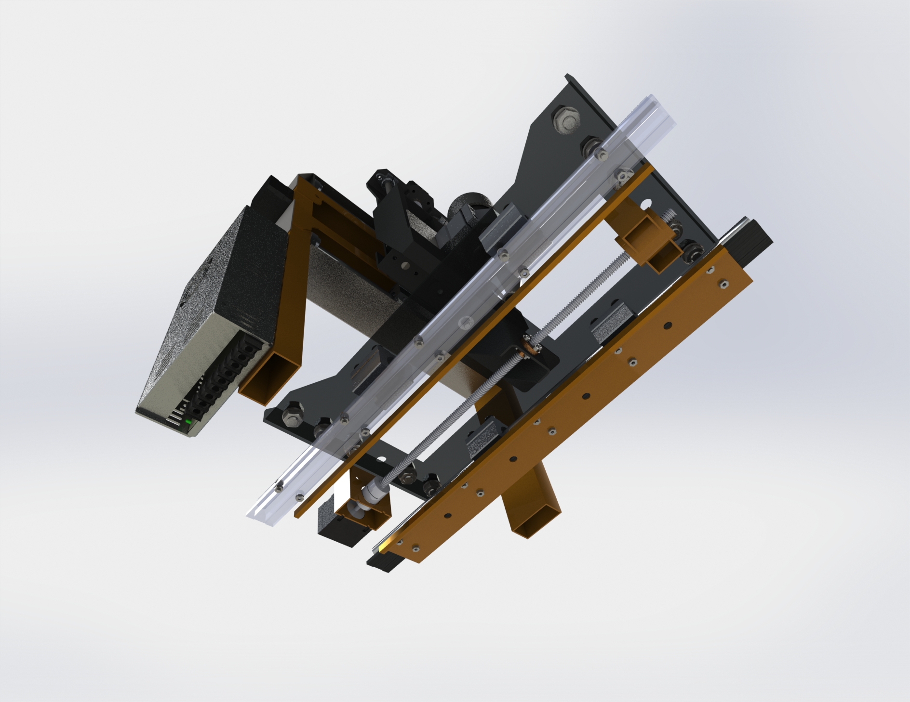
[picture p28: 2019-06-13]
renders/grupo.JPG

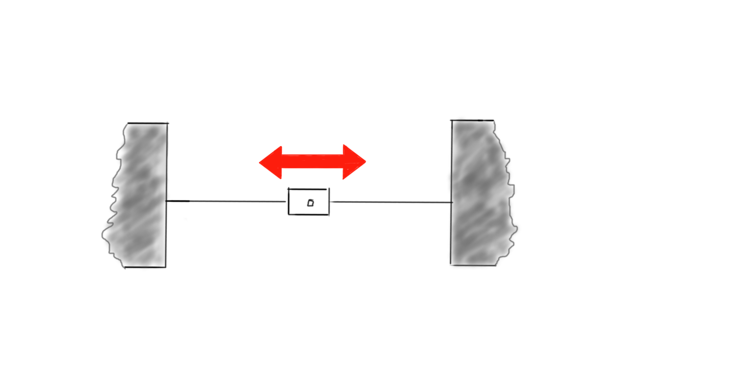
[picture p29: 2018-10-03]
esquema cinematico cnc1.tif

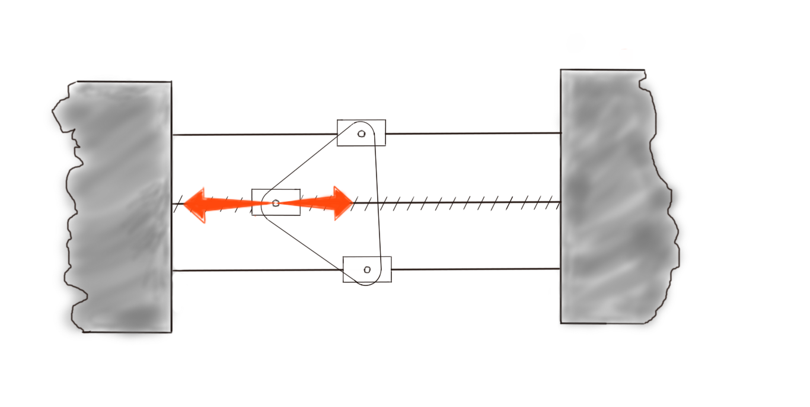
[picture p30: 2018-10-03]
esquema cinematico cnc4.tif

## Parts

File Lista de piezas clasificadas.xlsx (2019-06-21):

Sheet: General
N.º DE PIEZA | SUBENSAMBLAJE | MATERIAL | CANTIDAD | PROCESO DE MANUFACTURA | PROCESO DE MANUFACTURA2 | PROCESO DE MANUFACTURA3
base 2x1 laterales | Marco principal | Tubo 2"x1" | 2 | Corte de perfileria
base 2x1 frontal | Marco principal | Tubo 2"x1" | 2 | Corte de perfileria
soporte motor eje X | Marco principal | Tubo 2"x1" | 1 | Corte de perfileria | Taladrado
soporte rodamiento eje X | Marco principal | Tubo 2"x1" | 1 | Corte de perfileria | Taladrado
soporte transvarsal base | Marco principal | Angular 1" | 2 | Corte de perfileria | Taladrado
soporte vertical base eje Y (rodamiento) | Marco principal | Tubo 2"x1" | 1 | Corte de perfileria | Taladrado
soporte vertical base eje Y (motor) | Marco principal | Tubo 2"x1" | 1 | Corte de perfileria | Taladrado
asiento de rodamiento | Marco principal | Barra 1020 n2" | 2 | Maquinado | Torneado
tuerca m6 | Marco principal |  | 4
pata | Marco principal |  | 4
soporte superior marco | Marco principal | Angular "2 | 1 | Corte de perfileria
base lateral | Marco principal | Lamina espesor 4mm | 2 | Corte de lamina
soporte angular riel eje x | Marco principal | Angular 2" | 2 | Corte de perfileria | Taladrado
soporte superior 2 marco | Marco principal | Angular "2 | 1 | Corte de perfileria
perfil estructural aluminio base | Eje X | Perfil estructural aluminio | 7 | Corte de perfileria
rodamiento d12 perfil abierto | Eje X |  | 4
base eje X rediseñado | Eje X | Lamina 1020 2mm espesor | 1 | Corte de lamina | Torneado
bancada eje X | Eje X | Tubo 2"x2" | 1 | Corte de perfileria | Soldadura | Taladrado
viga longitudinal eje_y | Eje Y | Angular 1.5"x1.5" aluminio | 2 | Corte de perfileria
soporte transversal carro eje_y | Eje Y | Angular 1.5"x1.5" aluminio | 1 | Corte de perfileria | Taladrado
soporte transversal superior carro eje_y | Eje Y | Angular 1.5"x1.5" aluminio | 1 | Corte de perfileria | Taladrado
base para rodamientos eje y | Eje Y | Angular 2"x2" aluminio | 2 | Corte de perfileria
asiento de rodamiento tornillo eje z | Eje Y | Barra 2"n aluminio | 1 | Maquinado | Torneado
bancada eje Y | Eje Y | Lamina 5mm espesor aluminio | 1 | Corte de perfileria | Taladrado
soporte transversal carro eje z | Eje Z | Angular 2"x2" aluminio | 2 | Corte de perfileria
base para rodamientos eje z | Eje Z | Angular 2"x2" aluminio | 2 | Corte de perfileria
viga longitudinal eje z_izq | Eje Z | Angular 2"x2" aluminio | 1 | Corte de perfileria
viga longitudinal eje z_der | Eje Z | Angular 2"x2" aluminio | 1 | Corte de perfileria
soporte tranversal inferior eje_z | Eje Z | Angular 2"x2" aluminio | 1 | Corte de perfileria
Soporte a spindle arnes | Eje Z | Lamina 1.2mm espesor inox | 1 | Corte de lamina
base case electronica | Case electronica | Inox 308L | 1 | Corte de lamina
Case superior | Case electronica | Inox 308L | 1 | Corte de lamina
Lateral case superior | Case electronica | Inox 308L | 1 | Corte de lamina
case panel base | Case electronica | Inox 308L | 1 | Corte de lamina
case panel frontal | Case electronica | Inox 308L | 1 | Corte de lamina | Taladrado
bisagra conjunto | Case electronica | Inox 308L | 2
Case eje Y | Case eje Y | Inox 308L | 1 | Corte de lamina
Marco principal | CNC 4.0 |  | 1 | Soldadura
Eje X | CNC 4.0 |  | 1 | Soldadura
Eje Y | CNC 4.0 |  | 1 | Soldadura
Eje Z | CNC 4.0 |  | 1 | Soldadura | Fresado | Taladrado
Case electronica | CNC 4.0 | Inox 308L | 1 | Soldadura | Fresado | Taladrado
Case eje Y | CNC 4.0 | Inox 308L | 1 | Soldadura
TOTAL DE PIEZAS |  |  | 69

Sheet: Corte de perfileria
N.º DE PIEZA | MATERIAL | CANTIDAD | PROCESO DE MANUFACTURA
base 2x1 laterales | Tubo 2"x1" | 2 | Corte de perfileria
base 2x1 frontal | Tubo 2"x1" | 2 | Corte de perfileria
soporte motor eje X | Tubo 2"x1" | 1 | Corte de perfileria
soporte rodamiento eje X | Tubo 2"x1" | 1 | Corte de perfileria
soporte transvarsal base | Angular 1" | 2 | Corte de perfileria
soporte vertical base eje Y (rodamiento) | Tubo 2"x1" | 1 | Corte de perfileria
soporte vertical base eje Y (motor) | Tubo 2"x1" | 1 | Corte de perfileria
soporte superior marco | Angular "2 | 1 | Corte de perfileria
soporte superior 2 marco | Angular "2 | 1 | Corte de perfileria
perfil estructural aluminio base | Perfil estructural aluminio | 7 | Corte de perfileria
bancada eje X | Tubo 2"x2" | 1 | Corte de perfileria
viga longitudinal eje_y | Angular 1.5"x1.5" aluminio | 2 | Corte de perfileria
soporte transversal carro eje_y | Angular 1.5"x1.5" aluminio | 1 | Corte de perfileria
soporte transversal superior carro eje_y | Angular 1.5"x1.5" aluminio | 1 | Corte de perfileria
base para rodamientos eje y | Angular 2"x2" aluminio | 2 | Corte de perfileria
bancada eje Y | Lamina 5mm espesor aluminio | 1 | Corte de perfileria
soporte transversal carro eje z | Angular 2"x2" aluminio | 2 | Corte de perfileria
base para rodamientos eje z | Angular 2"x2" aluminio | 2 | Corte de perfileria
viga longitudinal eje z_izq | Angular 2"x2" aluminio | 1 | Corte de perfileria
viga longitudinal eje z_der | Angular 2"x2" aluminio | 1 | Corte de perfileria
soporte tranversal inferior eje_z | Angular 2"x2" aluminio | 1 | Corte de perfileria

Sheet: Corte de lamina
N.º DE PIEZA | MATERIAL | CANTIDAD | PROCESO DE MANUFACTURA
base eje Y rediseñado | Lamina 1020 2mm espesor | 1 | Corte de lamina
Soporte a spindle arnes | Lamina 1.2mm espesor inox | 1 | Corte de lamina

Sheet: Torneado
N.º DE PIEZA | MATERIAL | CANTIDAD | PROCESO DE MANUFACTURA
asiento de rodamiento | Barra 1020 n2" | 2 | Torneado
asiento de rodamiento tornillo eje z | Barra 2"n aluminio | 1 | Maquinado- Torneado

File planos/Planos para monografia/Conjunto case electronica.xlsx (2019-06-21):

N.º DE ELEMENTO | N.º DE PIEZA | MATERIAL | Solo case/CANTIDAD | PROCESO DE MANUFACTURA
1 | base case electronica | Inox 308L | 1 | Corte de lamina
2 | Case superior | Inox 308L | 1 | Corte de lamina
3 | Lateral case superior | Inox 308L | 1 | Corte de lamina
4 | case panel base | Inox 308L | 1 | Corte de lamina
5 | case panel frontal | Inox 308L | 1 | Corte de lamina
6 | bisagra conjunto | Inox 308L | 2

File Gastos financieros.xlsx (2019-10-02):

Mecánica
ITEM | DESCRIPCION | V. UNITARIO C$ | CANTIDAD (UND) | V. TOTAL C$ | FECHA DE COMPRA | V. TOTAL $
1 | 3X20 HEX. METRICO | C$3.07 | 4 | C$12.28 | 2016-12-03 | $0.42
2 | 6-32 UNIDAD A/PLANA | C$0.35 | 4 | C$1.40 | 2016-12-03 | $0.05
3 | 6-32 UNIDAD A/PLANA | C$0.35 | 24 | C$8.40 | 2016-11-22 | $0.29
4 | 3X35 ALLEN METRICO C/CIL | C$8.15 | 12 | C$97.80 | 2016-11-21 | $3.35
5 | PINTURA | C$2000.00 | 1 | C$2000.00 | 2019-05-22 | $60.70
6 | BOQUILLA DE CABEZAL | C$300.00 | 2 | C$600.00 | 2019-03-26 | $9.17
7 | PRENSA C | C$135.00 | 2 | C$270.00 | 2016-10-03 | $9.32
8 | BALINERA BOLA 1 HILERA 8X22X7 | C$126.17 | 3 | C$378.51 | 2016-11-01 | $13.01
9 | BALINERA BOLA 1 HILERA 8X22X7 | C$126.60 | 1 | C$126.60 | 2016-12-01 | $4.33
10 | FRESA 4 FILOS 9.0MM ESP 3/8 POLAND | C$319.00 | 1 | C$319.00 | 2017-01-30 | $10.84
11 | BROCA P/ROUTER 2 FILOS 3/8 | C$88.51 | 1 | C$88.51 | 2016-12-03 | $2.99
12 | BROCA METAL 3/8 HSS | C$192.11 | 1 | C$192.11 | 2016-12-03 | $6.58
13 | BROCA METAL 5/32 TITANIO | C$88.51 | 1 | C$88.51 | 2016-12-03 | $3.03
14 | BROCA METAL COBALTO 5/32 | C$103.31 | 2 | C$206.62 | 2016-12-12 | $8.03
15 | LINEAR BALL BEARING XYZ CNC | C$381.84 | 1 | C$381.84 | 2018-09-03 | $12.00
16 | LINEAR ROD RAIL SHAFT SUPPORT CNC | C$140.01 | 1 | C$140.01 | 2018-09-03 | $4.40
17 | SOLDADURA | C$729.61 | 1 | C$729.61 | 2016-11-25 | $25.00
18 | REPARACION DE EJE DE SPINDLE | C$200.00 | 1 | C$200.00 | 2019-03-26 | $6.12
19 | LINEAR GUIDE SUPPORT RAILS FOR CNC | C$938.70 | 2 | C$1877.40 | 2018-09-03 | $59.00
20 | BALL SCREW WITH 1204 FLANGE SINGLE BALL NUT | C$574.04 | 1 | C$574.04 | 2018-09-03 | $18.04
21 | LINEAR BEARING BUSHING | C$311.52 | 1 | C$311.52 | 2018-09-03 | $9.79
22 | LINEAR MOTION GUIDE RAIL ROUND ROD | C$630.04 | 2 | C$1260.08 | 2018-09-03 | 39.6
23 | SHAFT SUPPORT LINEAR RAIL | C$158.78 | 1 | C$158.78 | 2018-09-03 | $4.99
24 | LINEAR BALL BEARING BLOCK CNC | C$525.03 | 1 | C$525.03 | 2018-09-03 | $16.50
25 | LINEAR SHAFT RAIL | C$448.67 | 2 | C$897.33 | 2018-09-03 | $14.10
26 | CASE INOXIDABLE | C$9718.62 | 1 | C$9718.62 | 2019-01-15 | $300.00
27 | FRESA 4 FILOS 6.00 MM | C$450.00 | 1 | C$450.00 | 2019-04-27 | $13.70
28 | FRESA 4 FILOS 5 MM | C$250.00 | 1 | C$250.00 | 2019-04-27 | $7.61
29 | BALINERA BOLA 1 HILERA 8X22X7 | C$140.00 | 1 | C$140.00 | 2019-05-26 | $4.25
30 | BROCA DE COBALTO 3/8" | C$150.00 | 1 | C$150.00 | 2019-05-28 | $4.55
31 | BROCA DE COBALTO 1/2" | C$180.00 | 1 | C$180.00 | 2019-05-28 | $5.46
32 | BROCA DE COBALTO 8MM | C$120.00 | 1 | C$120.00 | 2019-05-28 | $3.64
33 | BROCAS HSS 1/4" | C$50.00 | 3 | C$150.00 | 2019-05-28 | $4.55
34 | BROCAS HSS 3/16" | C$30.00 | 3 | C$90.00 | 2019-05-28 | $2.73
35 | DISCOS DE CORTE | C$50.00 | 2 | C$100.00 | 2019-02-21 | $3.07
36 | DISCO FLAP | C$80.00 | 1 | C$80.00 | 2019-02-21 | $2.46
37 | DISCO DE ALAMBRE | C$200.00 | 1 | C$200.00 | 2019-02-21 | $6.14
38 | HOJAS DE SIERRA | C$50.00 | 4 | C$200.00 | 2019-02-21 | $6.14
39 | MANO DE OBRA PINTURA | C$2000.00 | 1 | C$2000.00 | 2019-05-22 | $60.70
40 | COSTOS DE ENVIO | C$2457.14 | 1 | C$2457.14 | 2018-09-03 | $77.22
 | TOTAL |  |  | C$27731.15 |  | $843.86
Electrónica
ITEM | DESCRIPCION | V. UNITARIO C$ | CANTIDAD (UND) | V. TOTAL C$ | FECHA DE COMPRA | V. TOTAL $
1 | KIT ARDUINO UNO | C$1550.00 | 1 | C$1550.00 | 2016-07-06 | $51.55
2 | CONCTAC CLEANER | C$331.21 | 1 | C$331.21 | 2016-10-29 | $11.39
3 | MULTIMETRO DIGITAL 500V AC TRUPER | C$352.51 | 1 | C$352.51 | 2016-11-21 | $13.79
4 | SPINDEL HEAD | C$3322.13 | 1 | C$3322.13 | 2016-11-14 | $114.00
5 | MOTORES (STEPPER) | C$728.50 | 3 | C$2185.50 | 2016-11-14 | $75.00
6 | KIT ARDUINO MEGA | C$2452.49 | 1 | C$2452.49 | 2019-03-26 | $75.00
7 | JUMPERS | C$3.50 | 20 | C$70.00 | 2019-05-15 | $2.13
8 | BORNERAS | C$65.00 | 10 | C$650.00 | 2019-05-15 | $19.75
9 | CARRIER DRAG CHAIN | C$309.93 | 2 | C$619.86 | 2018-09-03 | $19.48
10 | DRIVER A6600 | C$709.38 | 3 | C$2128.14 | 2018-09-03 | $66.88
11 | CABLES | C$120.00 | 5 | C$600.00 | 2019-05-15 | $18.23
12 | COSTO DE ENVIO | C$1272.80 | 1 | C$1272.80 | 2018-09-03 | $40.00
 | TOTAL |  |  | C$15534.64 |  | $507.19
Mano de Obra
ITEM | DESCRIPCION | V. UNITARIO C$ | CANTIDAD (DIAS) | V. TOTAL C$ | V. TOTAL $
1 | Almuerzo | C$60.00 | 128 | C$7680.00 | $232.73
2 | Pasajes autobus | C$10.00 | 128 | C$1280.00 | $38.79
3 | Agua | C$5.00 | 128 | C$640.00 | $19.39
 | TOTAL |  |  | C$19200.00 | $581.82
Gasto total
No | Tipo de Gastos | Total C$ | Total $
1 | Mecánica | C$27731.15 | $843.86
2 | Electrónica | C$15534.64 | $507.19
3 | Mano de Obra | C$19200.00 | $581.82
 | Total | C$62465.80 | $1932.86

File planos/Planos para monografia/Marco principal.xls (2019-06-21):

N.º DE ELEMENTO | N.º DE PIEZA | MATERIAL | Solo/CANTIDAD | PROCESO DE MANUFACTURA
1 | base 2x1 laterales | Tubo 2"x1" | 2 | Corte de perfileria
2 | base 2x1 frontal | Tubo 2"x1" | 2 | Corte de perfileria
3 | soporte motor eje X | Tubo 2"x1" | 1 | Corte de perfileria
4 | soporte rodamiento eje X | Tubo 2"x1" | 1 | Corte de perfileria
5 | soporte transvarsal base | Angular 1" | 2 | Corte de perfileria
6 | soporte vertical base eje Y (rodamiento) | Tubo 2"x1" | 1 | Corte de perfileria
7 | soporte vertical base eje Y (motor) | Tubo 2"x1" | 1 | Corte de perfileria
8 | asiento de rodamiento | Barra 1020 n2" | 2 | Torneado
9 | tuerca m6 |  | 4
10 | pata |  | 4
11 | soporte superior marco | Angular 2" | 1 | Corte de perfileria
12 | soporte superior 2 marco | Angular 2" | 1 | Corte de perfileria
13 | base lateral | Lamina espesor 4mm | 2 | Corte de lamina
14 | soporte angular riel eje x | Angular 2" | 2 | Corte de perfileria

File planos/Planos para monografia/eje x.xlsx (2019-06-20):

N.º DE ELEMENTO | N.º DE PIEZA | MATERIAL | CANTIDAD | PROCESO DE MANUFACTURA
1 | perfil estructural aluminio base | Perfil estructural aluminio | 7 | Corte de perfileria
2 | rodamiento d12 perfil abierto |  | 4
3 | base eje Y rediseñado | Lamina 1020 2mm espesor | 1 | Corte de lamina
4 | bancada eje X | Tubo 2"x2" | 1 | Corte de perfileria

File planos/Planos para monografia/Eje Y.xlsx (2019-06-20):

N.º DE ELEMENTO | N.º DE PIEZA | MATERIAL | CANTIDAD | PROCESO DE MANUFACTURA
1 | viga longitudinal eje_y | Angular 1.5"x1.5" aluminio | 2 | Corte de perfileria
2 | soporte transversal carro eje_y | Angular 1.5"x1.5" aluminio | 1 | Corte de perfileria
3 | soporte transversal superior carro eje_y | Angular 1.5"x1.5" aluminio | 1 | Corte de perfileria
4 | base para rodamientos eje y | Angular 2"x2" aluminio | 2 | Corte de perfileria
5 | asiento de rodamiento tornillo eje z | Barra 2"n aluminio | 1 | Maquinado- Torneado
6 | bancada eje Y | Lamina 5mm espesor aluminio | 1 | Corte de perfileria

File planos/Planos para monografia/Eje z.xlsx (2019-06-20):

N.º DE ELEMENTO | N.º DE PIEZA | MATERIAL | Solo estructura/CANTID AD | PROCESO DE MANUFACTURA
1 | soporte transversal carro eje z | Angular 2"x2" aluminio | 2 | Corte de perfileria
2 | base para rodamientos eje z | Angular 2"x2" aluminio | 2 | Corte de perfileria
3 | viga longitudinal eje z_izq | Angular 2"x2" aluminio | 1 | Corte de perfileria
4 | viga longitudinal eje z_der | Angular 2"x2" aluminio | 1 | Corte de perfileria
5 | soporte tranversal inferior eje_z | Angular 2"x2" aluminio | 1 | Corte de perfileria
6 | Soporte a spindle arnes | Lamina 1.2mm espesor inox | 1 | Corte de lamina

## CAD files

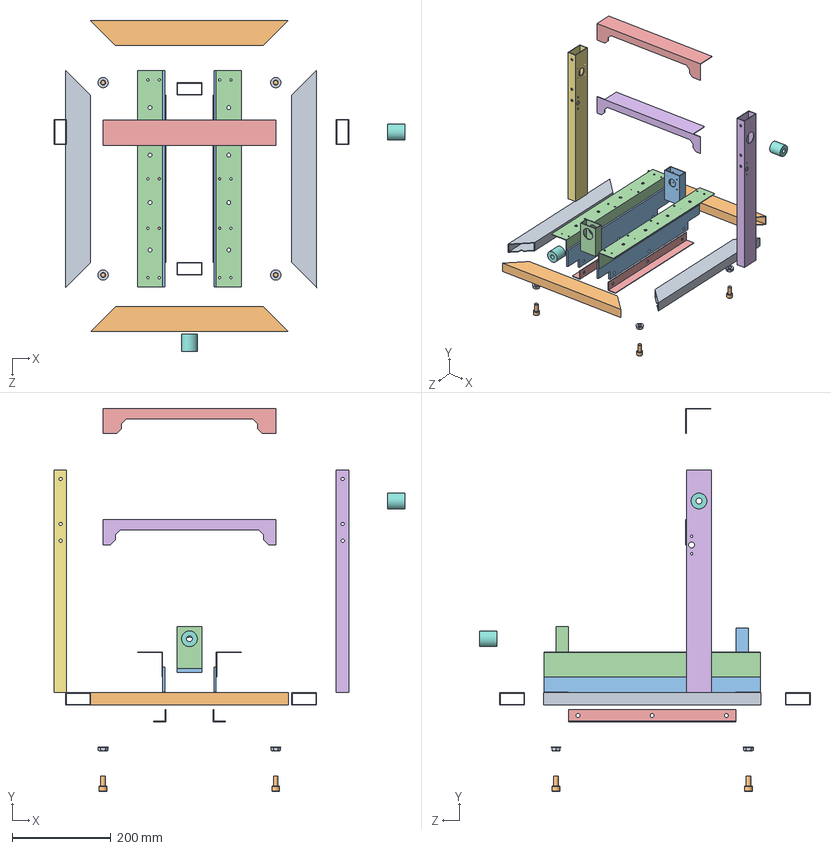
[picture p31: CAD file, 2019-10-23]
cnc DM2 final/marco 4.0.SLDASM
709.4 x 774.7 x 669.0 mm
base 2x1 laterales x 2
base 2x1 frontal x 2
soporte motor eje X
soporte rodamiento eje X
soporte transvarsal base x 2
soporte vertical base eje Y (rodamiento)
soporte vertical base eje Y (motor)
asiento de rodamiento x 2
tuerca m6 x 4
pata x 4
base lateral x 2
soporte angular riel eje x x 2
soporte superior marco
soporte superior 2 marco

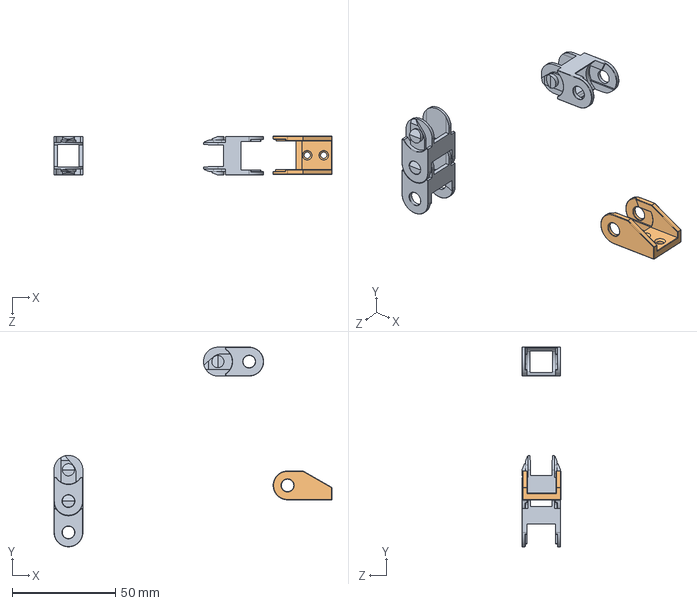
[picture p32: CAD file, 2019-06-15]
Prototipo 1/cadena.SLDASM
134.7 x 96.8 x 18.9 mm
esteira 15mm meio x 3
esteira 15mm ponta

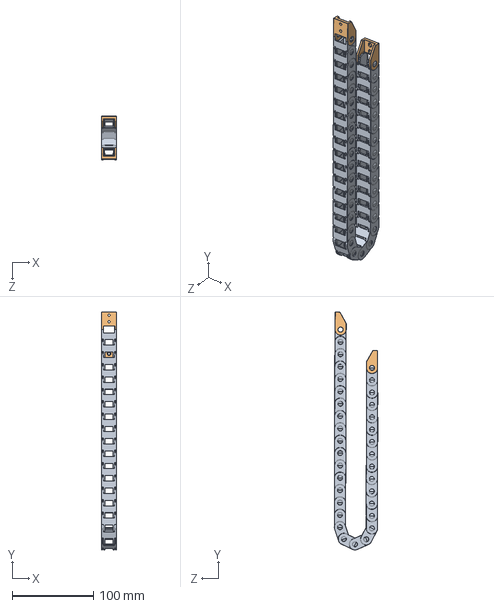
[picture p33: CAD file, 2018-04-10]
Prototipo 1/cable-drag-chain-wire-10x15mm-1.snapshot.2/esteira assy eixo y.SLDASM
18.8 x 292.6 x 53.5 mm
esteira 15mm meio x 33
esteira 15mm ponta x 2

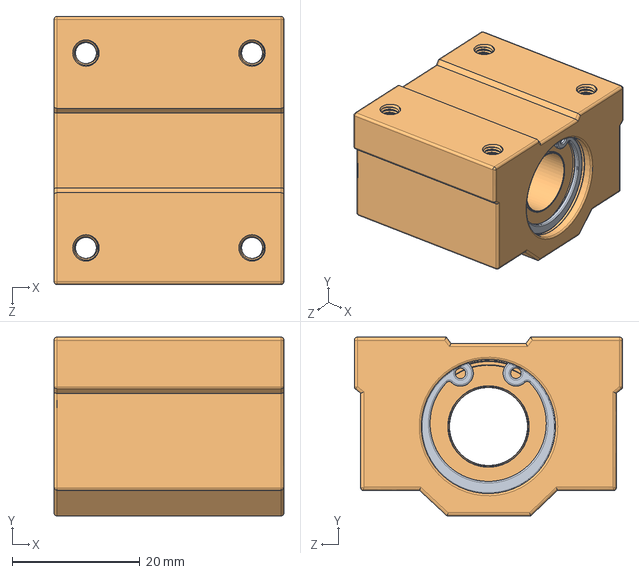
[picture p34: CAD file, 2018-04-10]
Prototipo 1/pillow-block-sc12uu-1.snapshot.2/PILLOW 12MM FINAL.SLDASM
36.0 x 28.0 x 42.0 mm
CLAMP x 2
pillow 12mm M4

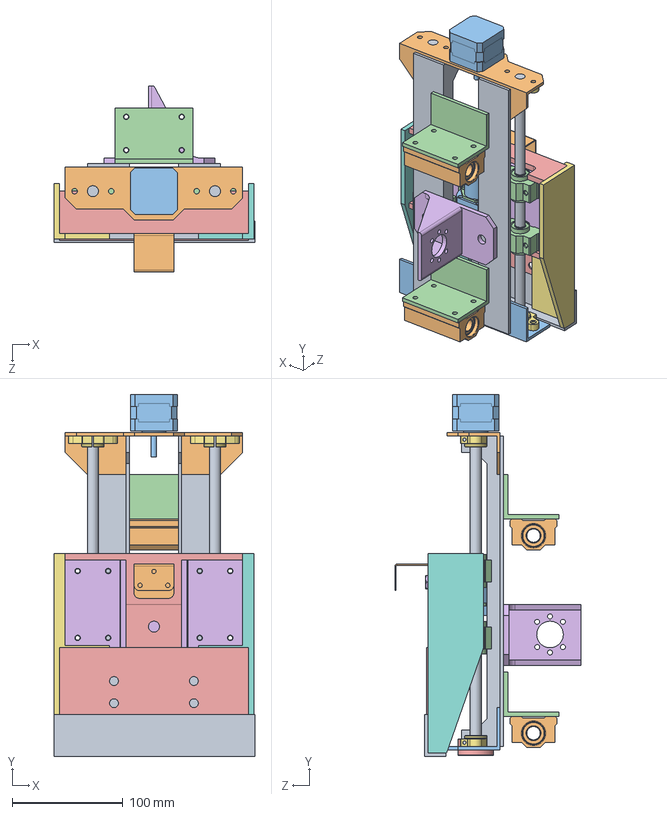
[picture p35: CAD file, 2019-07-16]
cnc DM2 final/carro eje y.SLDASM
181.0 x 326.2 x 168.0 mm
viga longitudinal eje_y x 2
soporte transversal carro eje_y
soporte transversal superior carro eje_y
base para rodamientos eje y x 2
asiento de rodamiento tornillo eje z
bancada eje Y
soporte guia 10mm x 4
rodamiento skf 8X22
eje y x 2
rodamiento d12 perfil cerrado x 2
nema 17-2
rodamiento d10 perfil cerrado x 4
soporte transversal carro eje z x 2
base para rodamientos eje z x 2
viga longitudinal eje z_izq
viga longitudinal eje z_der
soporte tranversal inferior eje_z
Soporte a spindle arnes
tuerca motriz
bancada eje z
base spindle
tornillo exagonal 8x20

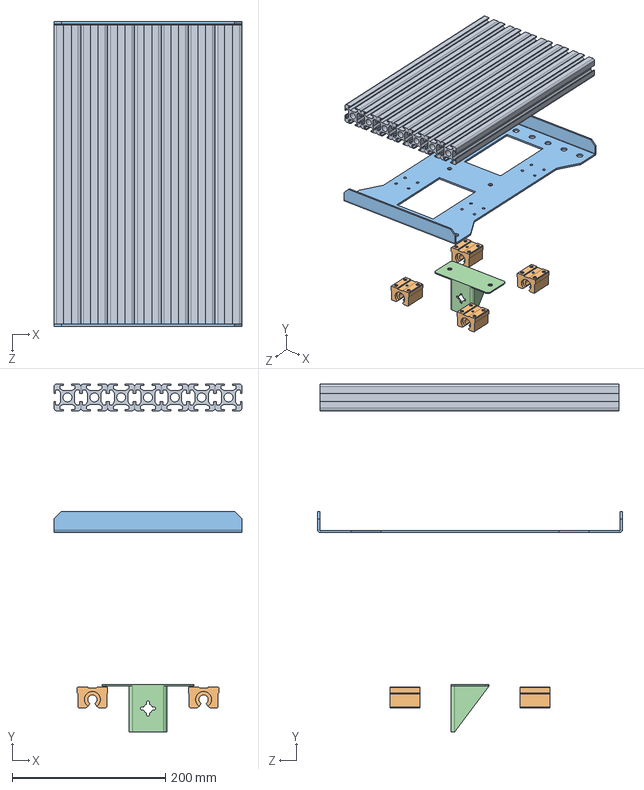
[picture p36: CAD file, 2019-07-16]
cnc DM2 final/cama de maquinado.SLDASM
245.0 x 453.8 x 397.5 mm
perfil estructural aluminio base x 7
rodamiento d12 perfil abierto x 4
base eje Y rediseñado
bancada eje X

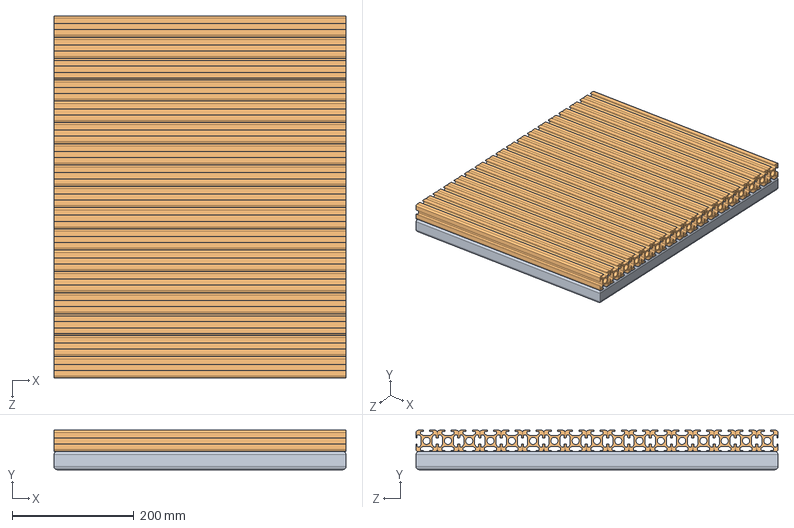
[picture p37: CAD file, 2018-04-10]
Prototipo 1/Base.SLDASM
480.0 x 65.0 x 595.0 mm
Marco base
perfil estructural aluminio base x 17

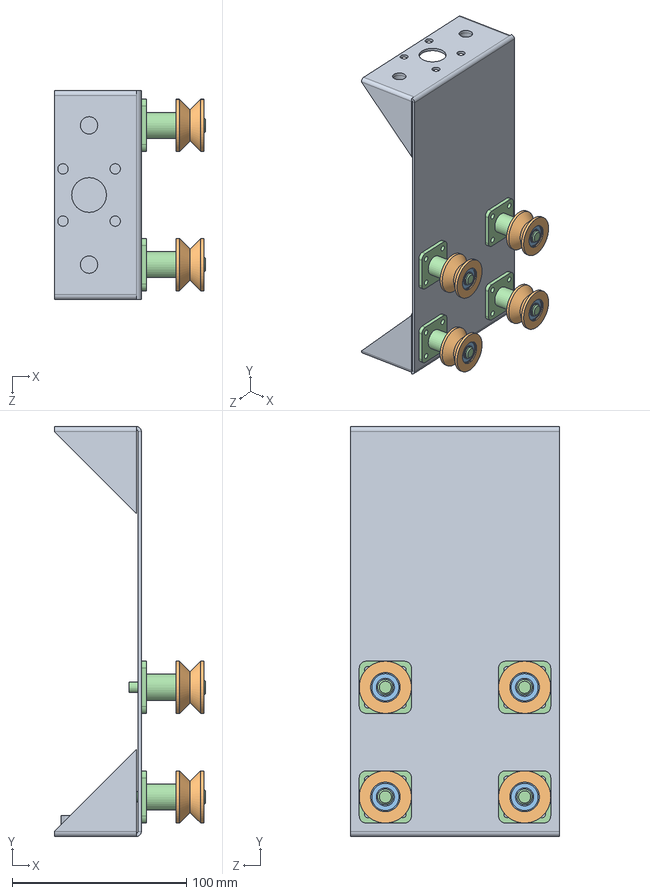
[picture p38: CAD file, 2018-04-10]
Prototipo 1/eje z.SLDASM
87.0 x 235.5 x 120.0 mm
base eje Z
rodillo eje Y x 4
Rodamiento 9x17 x 8
Eje de Rodillo en Y x 4

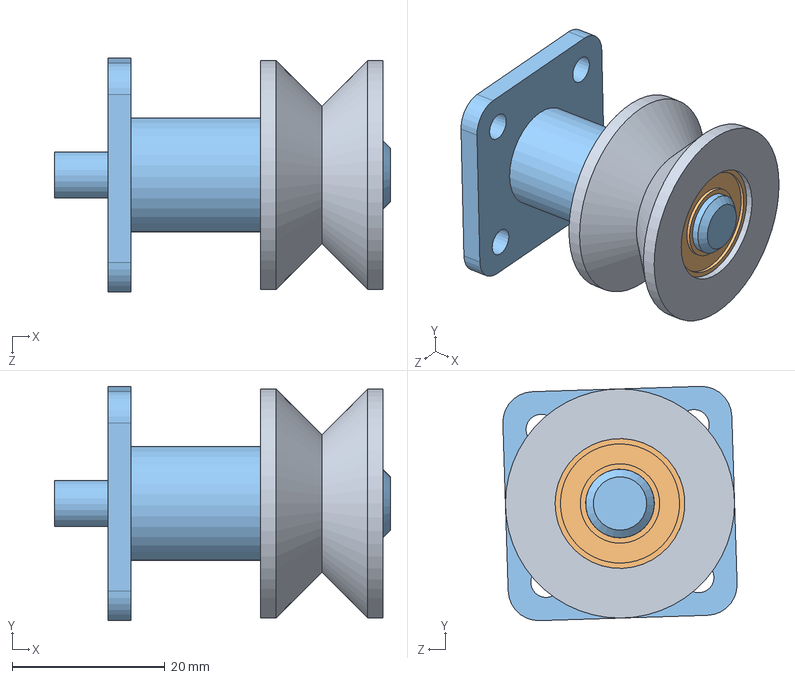
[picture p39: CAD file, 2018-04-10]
Prototipo 1/Conjunto rodillo eje Y.SLDASM
44.0 x 30.7 x 30.7 mm
rodillo eje Y
Rodamiento 9x17 x 2
Eje de Rodillo en Y

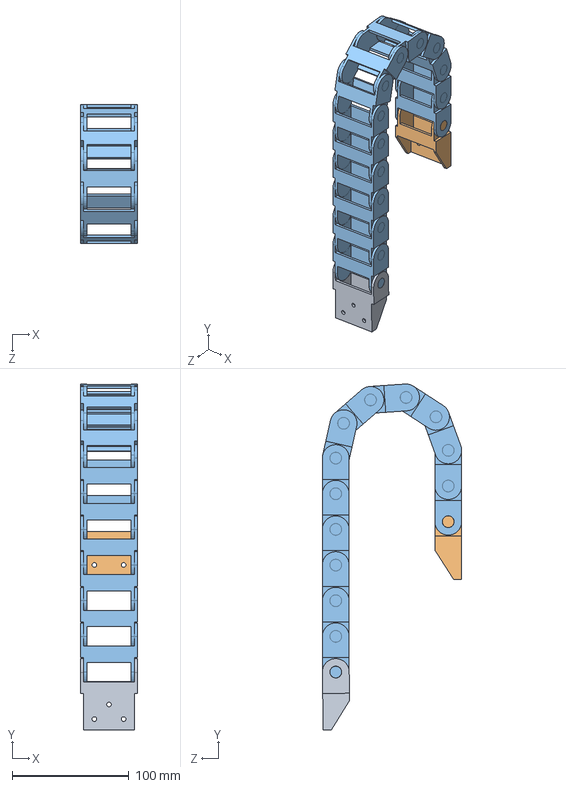
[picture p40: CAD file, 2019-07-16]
cnc DM2 final/Arnes electrico eje y.SLDASM
49.0 x 295.9 x 119.2 mm
endlink
startlink
drag chain link x 13

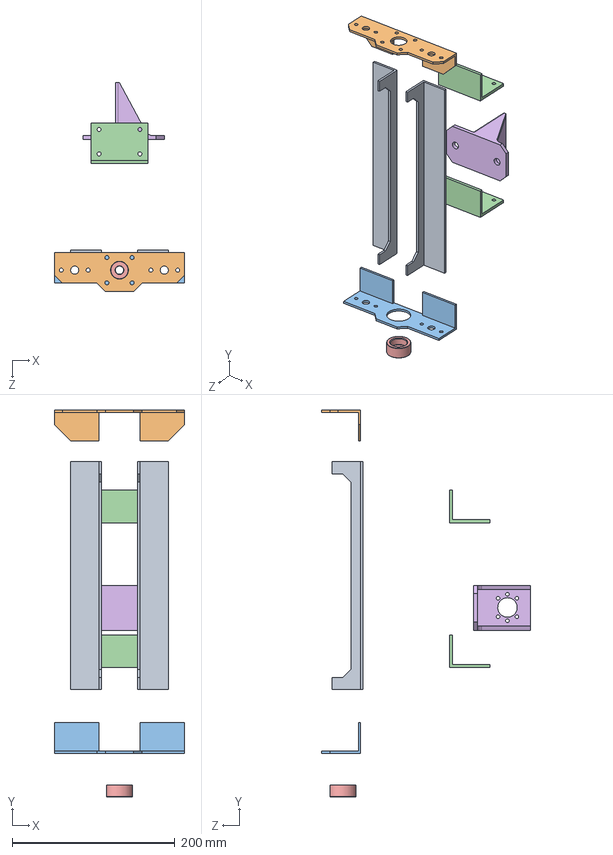
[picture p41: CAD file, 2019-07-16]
cnc DM2 final/Copia de Estructura base eje Y.sldasm
160.0 x 475.3 x 256.3 mm
viga longitudinal eje_y x 2
soporte transversal carro eje_y
soporte transversal superior carro eje_y
base para rodamientos eje y x 2
asiento de rodamiento tornillo eje z
bancada eje Y

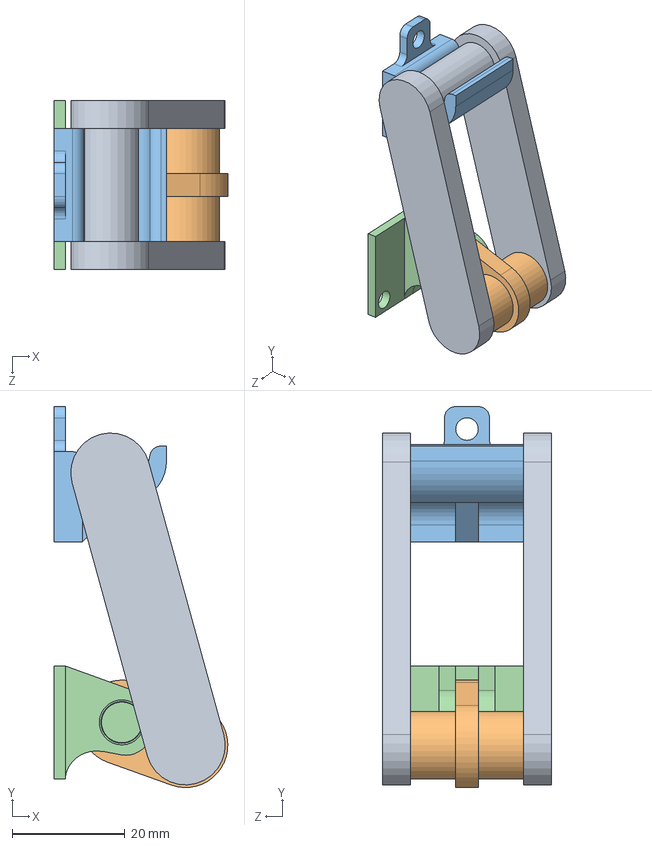
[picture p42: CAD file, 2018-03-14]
Prototipo 1/Seguro chino.SLDASM
30.8 x 67.5 x 30.0 mm
binario-2-3^Seguro chino
binario 2-2-4
seguro-2-1
chumacera-2-2

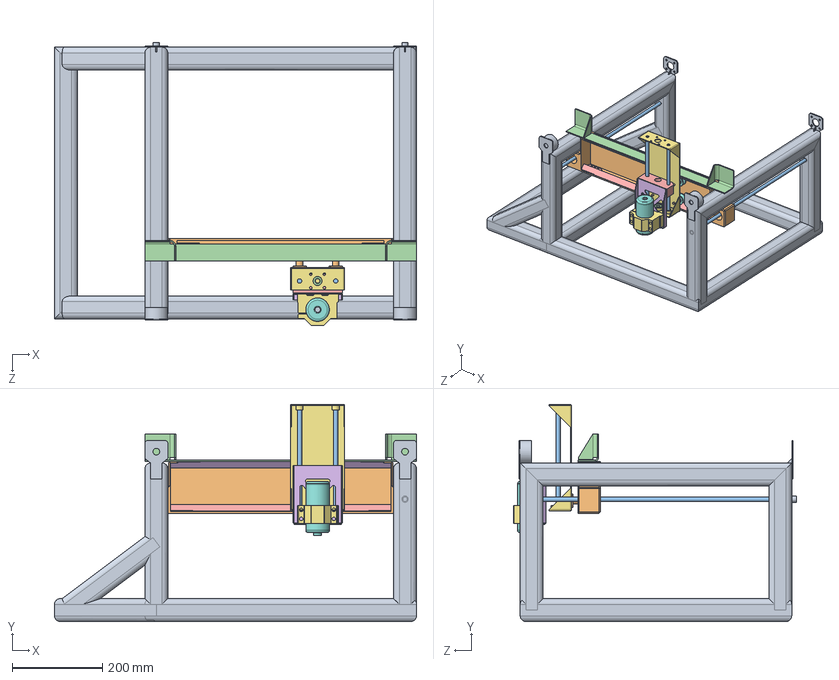
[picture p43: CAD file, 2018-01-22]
Prototipo 1/CNC 1.0.SLDASM
800.8 x 480.2 x 625.1 mm
bastidor
Puente
riel eje x x 2
soporte superior puente
Riel inferior eje Y
Riel superior eje Y
base eje Z
rodillo eje Y x 4
Rodamiento 9x17 x 8
Eje de Rodillo en Y x 4
Guia eje z x 2
rodamiento skf 10X25
Bancada eje z
soporte spindle
soporte de fijacion spindle
case spindle

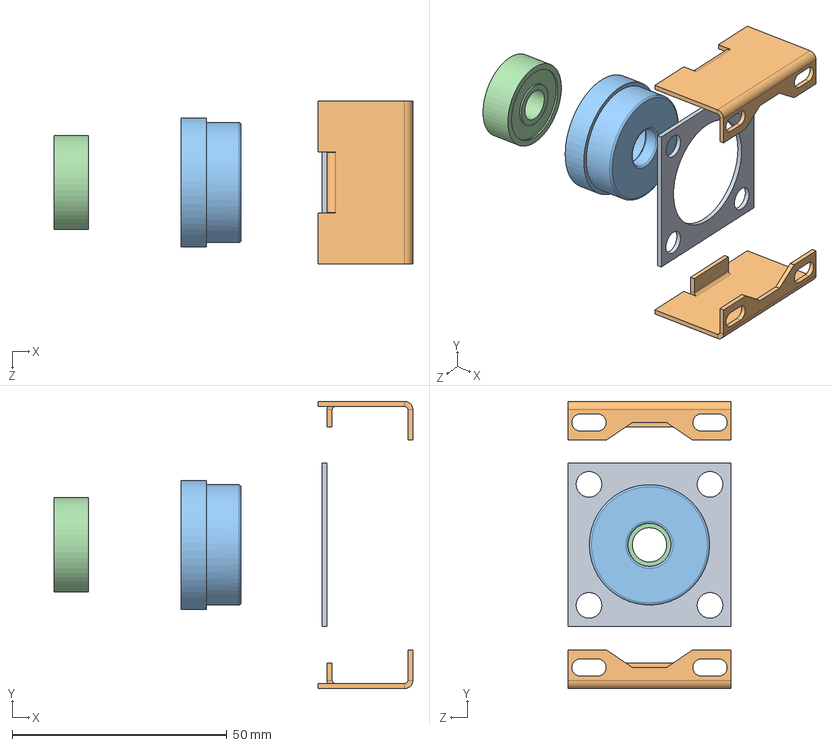
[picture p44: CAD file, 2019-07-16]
cnc DM2 final/soporte de eje-motor.SLDASM
83.6 x 66.9 x 38.0 mm
centro soporte motor
lateral soporte motor x 2
Asiento soporte de eje
rodamiento skf 8X22

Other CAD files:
cnc DM2 final/Cabezal eje Z.SLDASM
cnc DM2 final/Ensamblaje1.sldasm
cnc DM2 final/bisagra conjunto.SLDASM
cnc DM2 final/Arnes electrico eje z.SLDASM
Prototipo 1/4556T830_MOUNTING BRACKET.SLDPRT
Prototipo 1/Bancada eje z.SLDPRT
Prototipo 1/Base desmontable.SLDPRT
Prototipo 1/CPJC20-RD-5-10.SLDPRT
Prototipo 1/Cadena chino.SLDPRT
Prototipo 1/Eje de Rodillo en Y.SLDPRT
Prototipo 1/Guia eje z.SLDPRT
Prototipo 1/Marco base.SLDPRT
Prototipo 1/Puente.SLDPRT
Prototipo 1/Riel inferior eje Y.SLDPRT
Prototipo 1/Riel superior eje Y.SLDPRT
Prototipo 1/Rodamiento 10x30.SLDPRT
Prototipo 1/Rodamiento 9x17.SLDPRT
Prototipo 1/Seguro de la base 1.SLDPRT
Prototipo 1/Seguro/binario 2.SLDPRT
Prototipo 1/Seguro/binario.sldprt
Prototipo 1/Seguro/chumacera.sldprt
Prototipo 1/Seguro/seguro.sldprt
Prototipo 1/Soporte de tuerca eje Y.SLDPRT
Prototipo 1/base eje Z.SLDPRT
Prototipo 1/bastidor.SLDPRT
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

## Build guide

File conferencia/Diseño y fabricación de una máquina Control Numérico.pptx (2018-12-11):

## Diseño y fabricación de una máquina Control Numérico Computarizado (CNC) ROUTER de 3 ejes

UNI-FTI
Ingeniería Mecánica

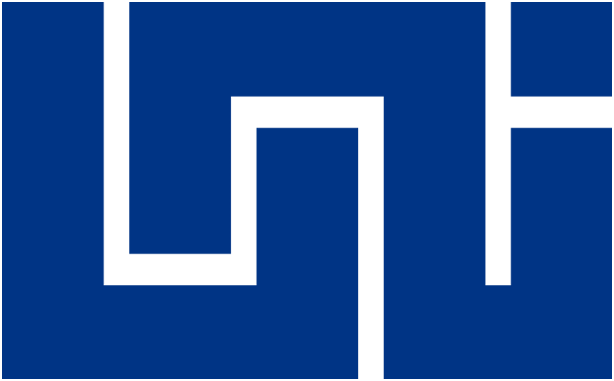
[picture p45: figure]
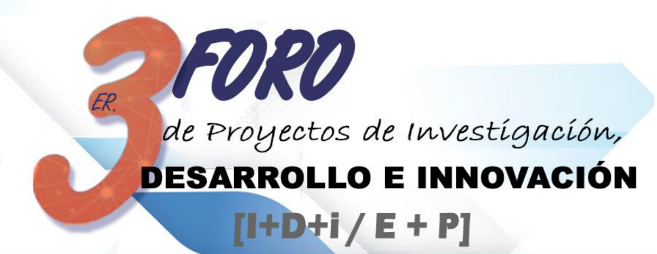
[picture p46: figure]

## Introducción

- Las máquinas de control numérico o CNC son el alma de la manufactura a gran escala por lo tanto se decidió hacer un esfuerzo en entender la tecnología con el fin de facilitar la comprensión de cómo y cuándo se deben utilizar, además de que se planteó una metodología de diseño mecánico la cual se ha ido refinando a lo largo de los proyectos en los que se han trabajado, dejando en esta investigación las conclusiones de cómo se debe elaborar un producto, en este caso un CNC siendo este estudio un arma de doble filo en donde se plantean los medios (Manufactura en máquinas CNC) para llevar a cabo el fin (Producto) que se proponga.


## Definición

- El control numérico computarizado es el uso de una computadora para controlar y monitorear los movimientos de una máquina herramienta.
- Todas las máquinas CNC comparten una característica en común: tienen dos o más direcciones programables de movimiento llamadas ejes.

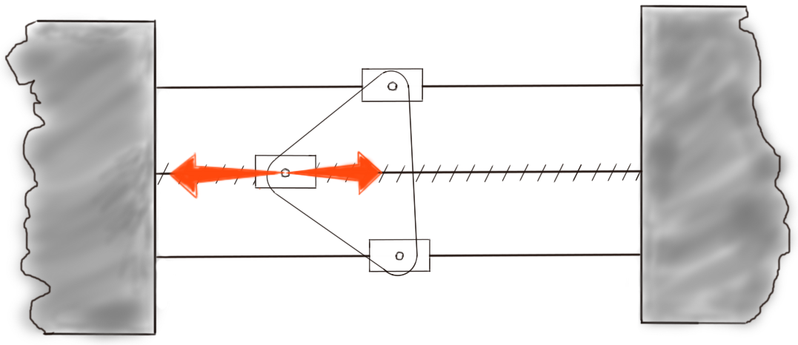
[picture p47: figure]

## Aplicación

Automatización de la preparación de la documentación constructiva y tecnológica: impresión, trazado de gráficos diagramas de bloques y circuitos eléctricos.
Automatización de la preparación tecnológica de la fabricación, construcción de fotomascaras para elementos semiconductores, circuitos integrados, impresión de circuitos integrados, etc.
Automatización de las operaciones tecnológicas en las que se realiza el mecanizado de metales: torneado, refrentado, taladrar, aserrar, fusionar, punzar, electro-erosión, tecnología, laser etc.
Automatización de las operaciones de medición del control en las cuales se definen las dimensiones de detalle mecánico.

## Metodología

Reconocimiento de la necesidad

Aislamiento de los factores que influyen en el problema

Propuestas de solución

Optimización

Evaluación técnica

Cubre las necesidades cliente

si

No

Presentación

## Metodología / Diseño

- Con el fin de agilizar el proceso de diseño se propone el uso de programas CAD/CAM dado que facilita las fases de evaluación y optimización de los productos diseñados.
- Programas como Solidworks, Inventor o Fusión 360 son muy buenas opciones.

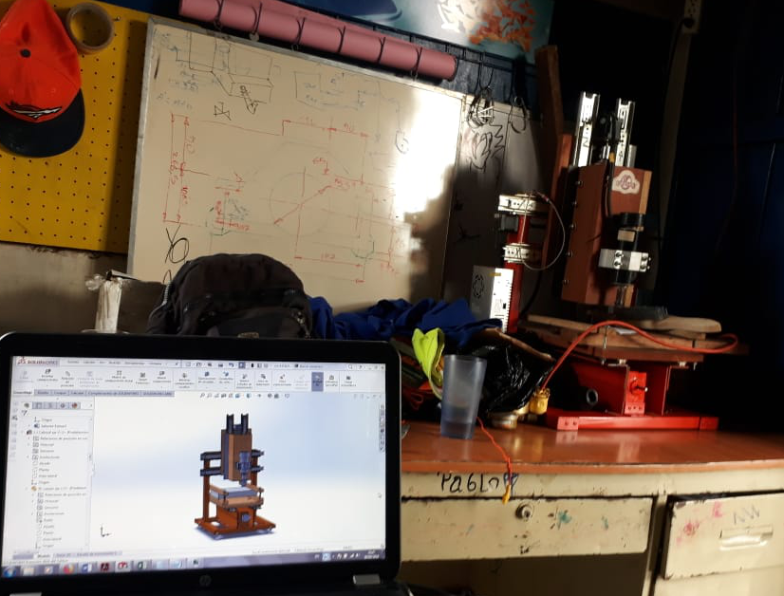
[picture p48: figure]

## Metodología / Manufactura

- Todo buen diseño contempla la facilidad de manufactura sin sacrificar la funcionalidad del dispositivo.
- La clave es seleccionar los procesos de fabricación adecuados; y esa es la razón por la que se decidió construir un CNC, debido a la versatilidad que este ofrece.

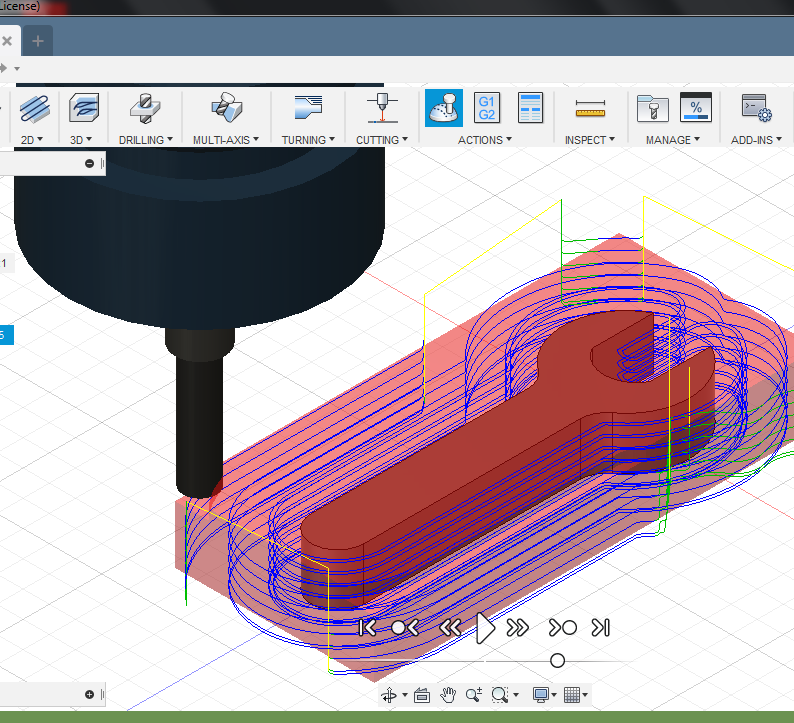
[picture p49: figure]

## Metodología / Control de datos

- A medida que la complejidad de los proyectos va aumentado se va haciendo necesaria una mayor cantidad de iteraciones para poder lograr los objetivos deseados en los productos, por lo tanto, en este proyecto se ha implementado un control de versiones (GIT) a fin de documentar el proyecto de comienzo a fin y monitorear el avance.

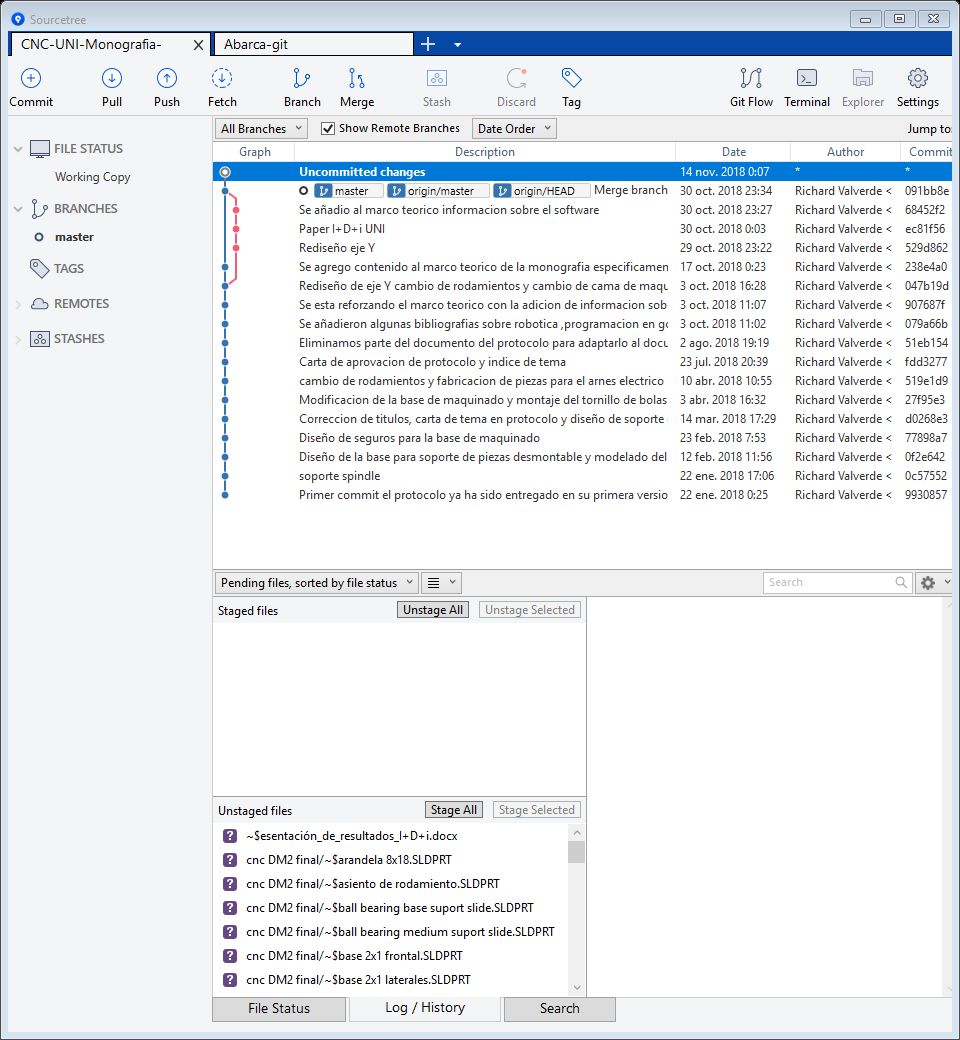
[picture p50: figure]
Sourcetree

## Metodología / Administración

No se puede medir lo que no se ha planeado y dada esta premisa se ha decidido emplear una herramienta de administración de personal a fin de agilizar los diferentes procesos que conlleva el diseño y fabricación de una maquina.

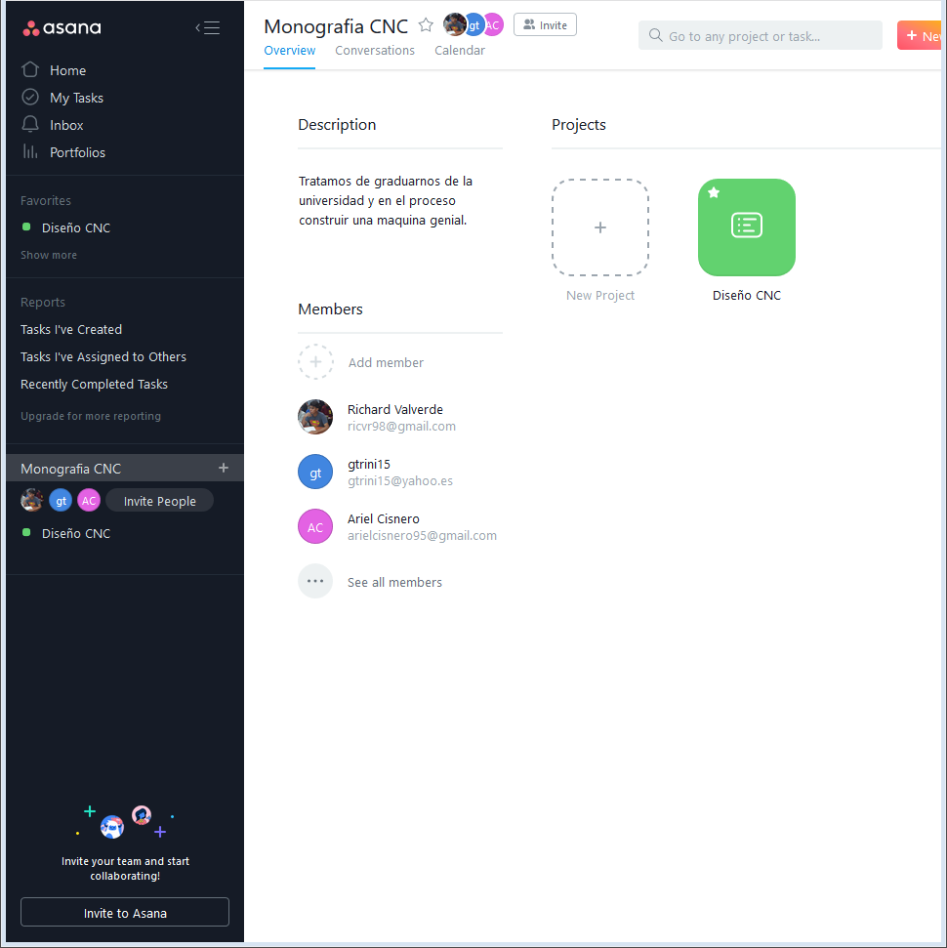
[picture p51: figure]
Monografia CNC Team - Asana - Mozilla Firefox

## Resultados(parciales)

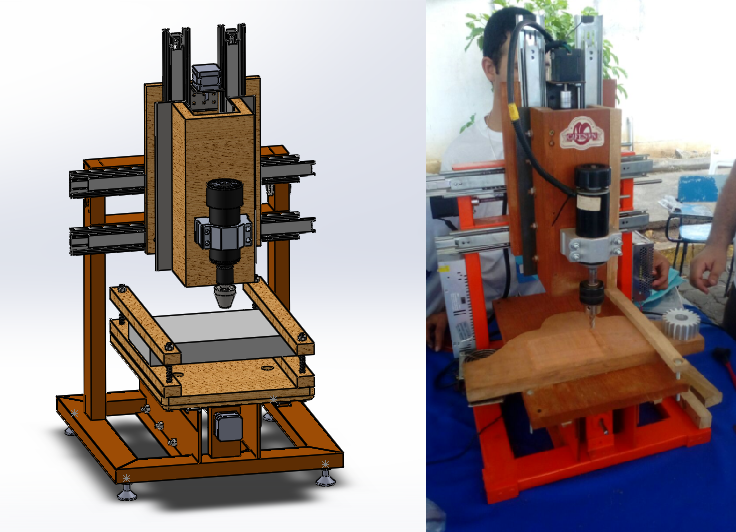
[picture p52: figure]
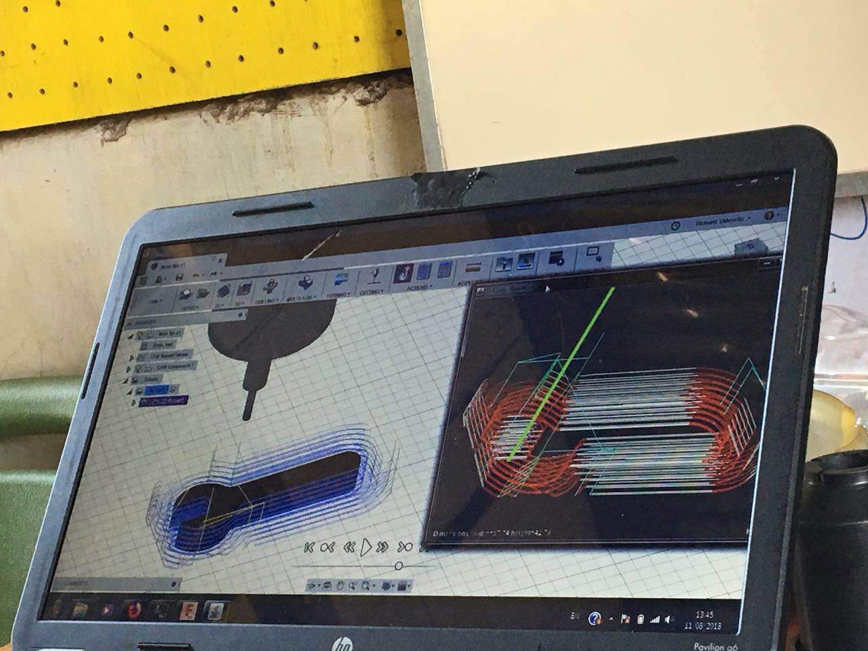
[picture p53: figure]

## Piezas fabricadas

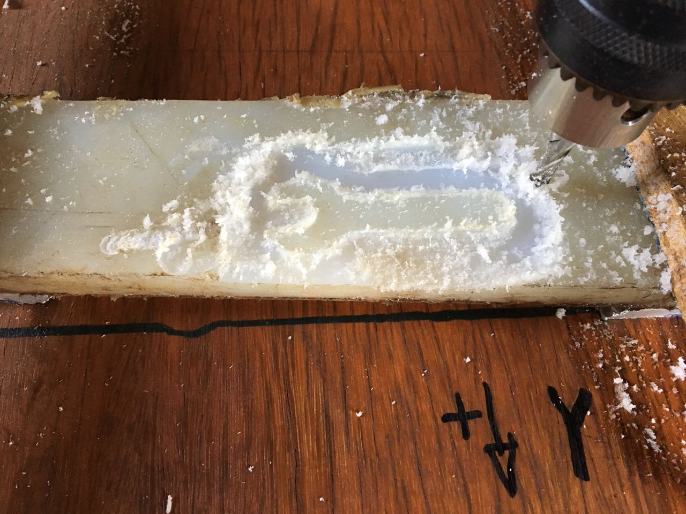
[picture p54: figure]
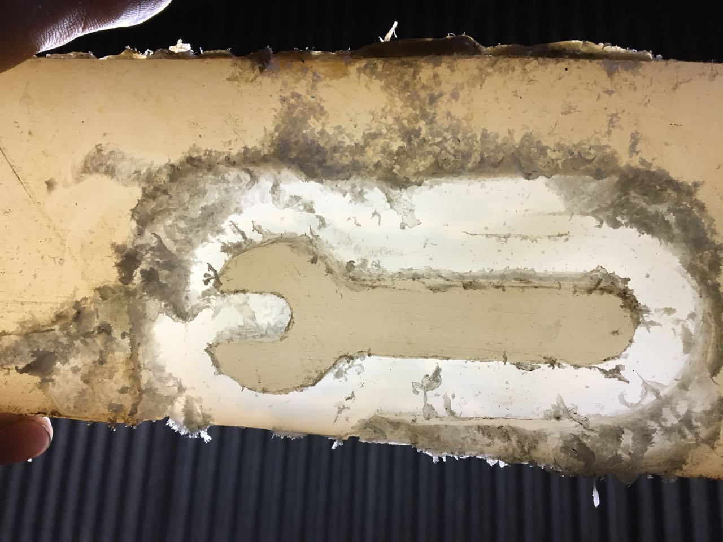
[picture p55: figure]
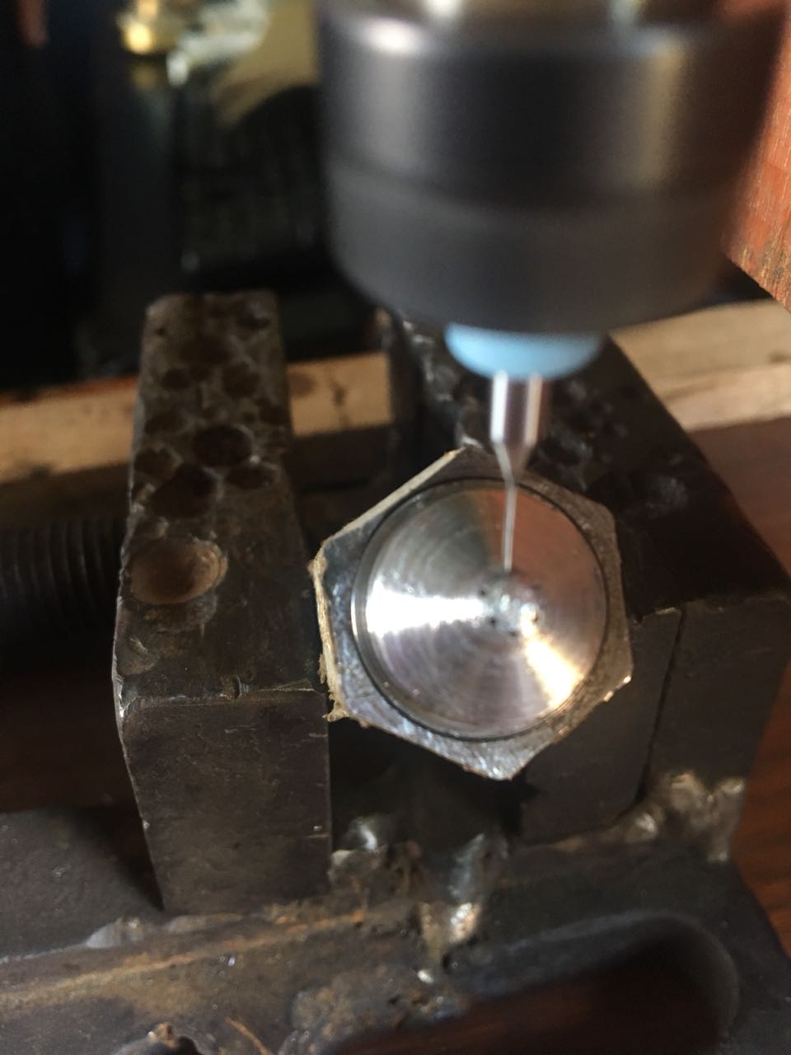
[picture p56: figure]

## FIN

Muchas gracias por su atención

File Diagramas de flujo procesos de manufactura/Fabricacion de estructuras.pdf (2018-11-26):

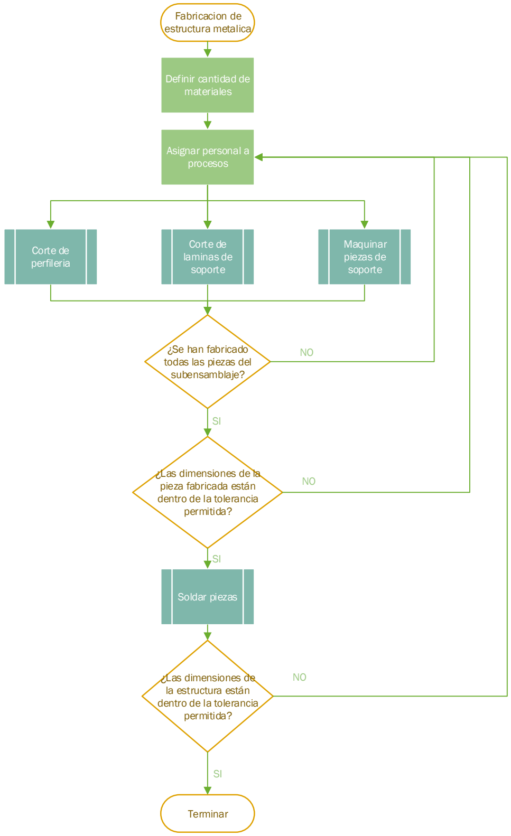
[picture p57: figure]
Fabricacion de estructura metalica; Terminar; Definir cantidad de materiales; Asignar personal a procesos; Corte de perfileria; Corte de laminas de soporte; Maquinar piezas de soporte; ¿Se han fabricado todas las piezas del subensamblaje?; ¿Las dimensiones de la pieza fabricada están dentro de la tolerancia permitida?; Soldar piezas; ¿Las dimensiones de la estructura están dentro de la tolerancia permitida?

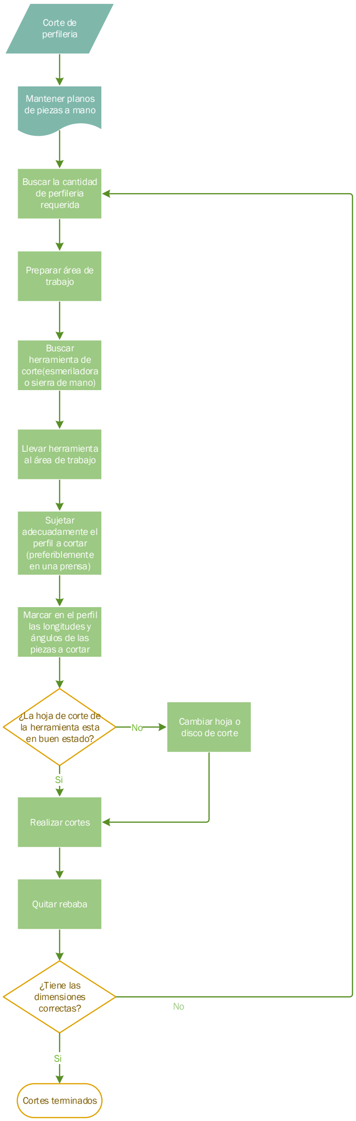
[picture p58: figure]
Corte de perfileria; Buscar la cantidad de perfileria requerida; Mantener planos de piezas a mano; Preparar área de trabajo; Buscar herramienta de corte(esmeriladora o sierra de mano); Llevar herramienta al área de trabajo; Sujetar adecuadamente el perfil a cortar (preferiblemente en una prensa); Marcar en el perfil las longitudes y ángulos de las piezas a cortar; ¿La hoja de corte de la herramienta esta en buen estado?; Realizar cortes; Cambiar hoja o; disco de corte; Quitar rebaba; ¿Tiene las dimensiones correctas?; Cortes terminados

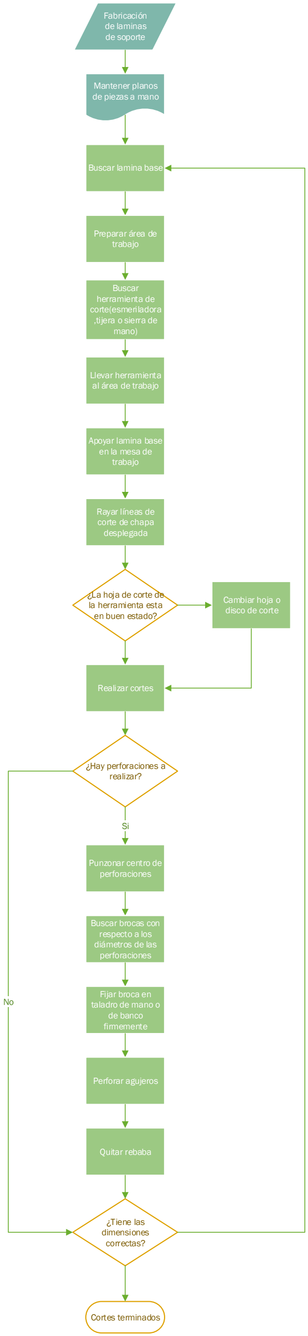
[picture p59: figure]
Fabricación de laminas de soporte; Mantener planos de piezas a mano; Buscar lamina base; Preparar área de trabajo; Buscar herramienta de corte(esmeriladora ,tijera o sierra de mano); Llevar herramienta al área de trabajo; Apoyar lamina base en la mesa de trabajo; Rayar líneas de corte de chapa desplegada; ¿La hoja de corte de la herramienta esta en buen estado?; Cambiar hoja o disco de corte; Realizar cortes; Quitar rebaba; ¿Tiene las dimensiones correctas?; Cortes terminados; Punzonar centro de perforaciones; Buscar brocas con respecto a los diámetros de las perforaciones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

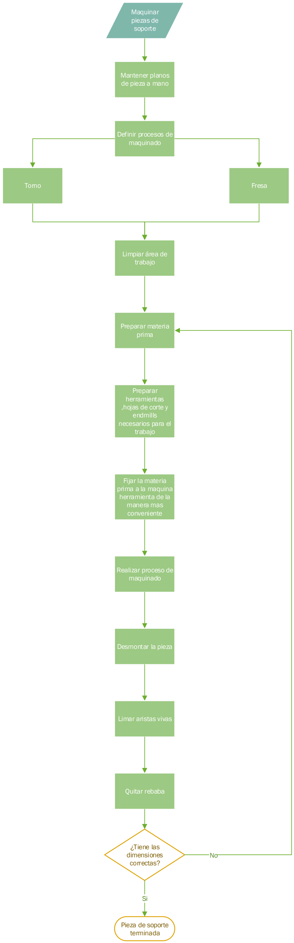
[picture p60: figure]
Maquinar piezas de soporte; Mantener planos de pieza a mano; Definir procesos de maquinado; Torno; Fresa; Limpiar área de trabajo; Preparar materia prima; Preparar herramientas ,hojas de corte y endmills necesarios para el trabajo; Fijar la materia prima a la maquina herramienta de la manera mas conveniente; Realizar proceso de maquinado; Desmontar la pieza; Limar aristas vivas; Quitar rebaba; ¿Tiene las dimensiones correctas?; Pieza de soporte terminada

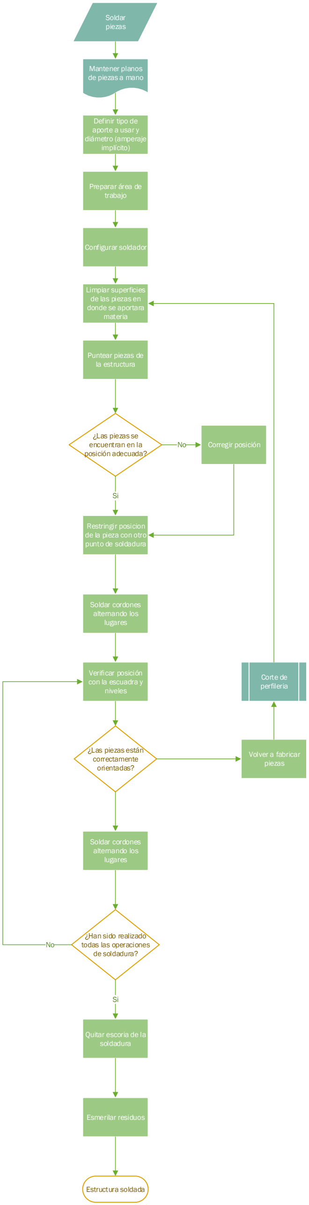
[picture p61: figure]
Soldar piezas; Mantener planos de piezas a mano; Definir tipo de aporte a usar y diámetro (amperaje implícito); Preparar área de trabajo; Configurar soldador; Limpiar superficies de las piezas en donde se aportara materia; Puntear piezas de la estructura; ¿Las piezas se encuentran en la posición adecuada?; Restringir posicion de la pieza con otro punto de soldadura; Corregir posición; Soldar cordones alternando los lugares; ¿Las piezas están correctamente orientadas?; Verificar posición con la escuadra y niveles; Volver a fabricar piezas; Corte de perfileria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

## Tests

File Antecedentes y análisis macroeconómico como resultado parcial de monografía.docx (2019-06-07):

# Antecedentes y análisis macroeconómico como resultado parcial de monografía “Diseño de router CNC de 3 ejes”

UNI RUPAP Facultad de Tecnologías de la Industria (FTI)

Autores: Richard Valverde Tutora: Ing. Mary Triny Gutiérrez

Ariel Cisnero

# 1. Antecedentes

Actualmente en Nicaragua no se ha encontrado información relacionada a alguna persona o empresa que haya construido o estén construyendo un CNC router sin embargo hay empresas que distribuyen dichas maquinas; empresas como “Copre” que ofrece variedad de máquinas, un alto stock de repuestos, así como capacitaciones a los operarios.

Según lo investigado encontramos que en el año 2011 se aprobó en el presupuesto nacional de la republica la compra de 4 CNC, 8 fresadoras y 42 tornos (Hacienda, 2011) los cuales parcialmente fueron distribuidos al centro CEFNIHSB (Centro estudiantil de formación Nicaragüense Holandés Simón Bolívar) completándose así la instalación de 8 máquinas de control numérico de manufactura Coreana .Al día de hoy no hemos podido encontrar curso alguno que se imparta en este centro sobre manufactura en maquinaria CNC o relacionados en estas instalaciones.

Es entendible el hecho de la carencia de información referente al diseño de estas máquinas localmente, debido a la complejidad que presenta la construcción de CNC router aun así el concepto de CNC es muy amplio, sin embargo, un tipo de maquina muy parecida que trabaja bajo los mismos principios son las impresoras 3D, máquinas de las cuales si hay información.

Según el periódico la prensa la primera vez que se ha mencionado una impresora 3D fue en el año 2013

(Sepúlveda, La prensa, 14 de abril 2015) ¨A comienzos del 2015, el ingeniero Enrique Aguilar recibió un mensaje a través de Facebook que le llamó la atención. Un hombre de Jinotega le preguntaba si podía ayudarlo a imprimir en 3D una prótesis de mano para su hijo de 6 años.

En 2013 Aguilar había comprado una impresora 3D, con la que recorrió universidades y ferias en Nicaragua para enseñar cómo funcionan estas máquinas y los usos que se le puede dar.

Ese mismo año Aguilar recibió el Premio Nacional a la Innovación del Consejo Nicaragüense de Ciencia y Tecnología (CONICYT), por ser el primer emprendedor nacional en incursionar en este tipo de impresión.

Luego según la misma publicación se informa que el siguiente caso proviene de unos estudiantes de postgrado que al no poder materializar satisfactoriamente su proyecto final no tuvieron otra alternativa que comprar una impresora 3D, según el periódico la prensa.

(Sepúlveda, 2015) El año pasado, mientras cursaba un posgrado de Arquitectura Contemporánea, Xóchitl Méndez comenzó a averiguar sobre impresión 3D en Nicaragua, ya que el diseño para su maqueta final era muy complicado de hacer de otra forma.

"Investigué aquí en Nicaragua y me di cuenta que no había, así que luego lo que hice fue cotizar en Costa Rica. Sin embargo, el costo era muy alto porque tenía que ir a traerla, además del costo de la maqueta. Ahí fue cuando decidí investigar sobre el costo de las impresoras y si podía venir a tiempo para la presentación final", narra Méndez.

Con un compañero decidieron invertir en una de estas máquinas, la que ahora tienen en su oficina de Motion Design, una empresa de diseño y arquitectura que además ofrece el servicio de impresión 3D para quienes necesiten hacer prototipos o maquetas.

Más reciente en una colaboración entre estudiantes de ingeniería electrónica e ingeniería en computación han fabricado su propia impresora 3D obteniendo buenos resultados logrando la fabricación de piezas en plásticos con buena calidad. (Anonimo, foroelectronico, 2016) Hasta el momento según investigaciones esa es toda la información disponible a cerca de la utilización o fabricación de estas máquinas en Nicaragua.

# 2. Macroeconomía

“El objetivo de las universidades es capacitar a los profesionales que necesita el mercado laboral nacional”

Esta frase define el sistema con el que actualmente se deciden cuáles son las habilidades que debería tener cada profesional y parcialmente está bien, pero creemos que debería haber un cambio de enfoque argumentado en los recursos que el país posee y en los fundamentos económicos para determinar cómo el país puede crear la mano obra correcta.

“El objetivo de las universidades es capacitar a los profesionales necesarios para el desarrollo del país”

La primera frase se enfoca en cumplir las expectativas de las empresas instaladas actualmente mientras que la segunda frase se centra en hacer lo necesario para generar productos con valor agregado sean bienes o servicios en pro del desarrollo del país.

Podríamos decir que la primera frase apuesta al pasado y la segunda frase apuesta hacia el futuro y aunque el futuro es incierto la clave del éxito reside en tomar la mayor cantidad de información disponible para tomar decisiones para el futuro.

Primero vamos a comenzar por definir cuáles son los sectores productivos de un país.

Sector primario: Está conformado por empresas cuyo principal giro económico consiste en la extracción y/o producción de materias primas.

Sector secundario: Consiste en empresas que se dedican a procesar materias primas con el fin de convertirlas en productos terminados o semiterminados.

Sector terciario: Las empresas que se encuentran en este sector se dedican a ofrecer servicios tales como los mostrados en el diagrama anteriormente expuesto.

Desde el punto de vista económico los países logran sostener la gestión pública a partir de las recaudaciones de impuestos que se generan a través de todas transacciones dadas por las diferentes actividades económicas del país.

Por lo tanto, podemos afirmar que gran parte del desarrollo de un país reside en el tipo de empresas instaladas en el mismo.

En todo país se requiere de la existencia de estos tres sectores para el funcionamiento de las actividades económicas ya sea en menor o mayor medida. La proporción ideal depende mucho de los recursos de los que el país posea ya sea como materia prima o como mano de obra capacitada (tangibles o intangibles) y como estos son variables en el tiempo no se puede hablar de una proporción constante idónea sobre las actividades que debería efectuar un país.

Aun así, se puede plantear un plan de desarrollo que permita optimizar el uso de los recursos en la medida de generar con los mismos una mayor cantidad de valor agregado.

En el grafico podemos observar (BCN, 2018) cual es la proporción actual de los sectores productivos de Nicaragua y como estos han evolucionado desde 2006 hasta el último año concluido fiscalmente en el cual podemos observar que la proporción se mantiene a lo largo de los años siendo el sector terciario dominante debido a que en él se atiende el servicios que son parcialmente del sector público tales son la salud, la educación y el transporte los cuales tienen un impacto notable debido a las políticas de inversión pública.

Con el objetivo de facilitar la visualización de los datos se ha anexado otro grafico en el cual se ha subdividido el sector terciario en público y privado siendo terciario publico toda aquella institución encargada de ofrecer servicios públicos mientras que los terciarios privados como su nombre lo indica se encargan de ofrecer servicios privados tales como los restaurantes, hotelería y telecomunicaciones.

Según se puede observar cualquiera de los sectores que tienen relevancia real (sector primario, secundario y terciario privado) en el aporte al PIB son inferiores al sector terciario público y realmente esto se explica debido al pobre desarrollo del sector secundario el cual debería encargarse de procesar las materias primas que se produzcan en el país para que posteriormente sean comercializadas por las empresas de los sectores terciarios privados.

El objetivo de todo este análisis con respecto al tema de la monografía es hacer énfasis en que la universidad tiene que capacitar profesionales con el fin de convertir a Nicaragua en un destino mucho más competitivo desde el punto de vista industrial para los inversionistas, además también de que se creen empresas en torno a las nuevas habilidades que se puedan desarrollar para generar valor agregado.

La industria revoluciona la economía de los países que la dominan y un punto de inflexión en cualquier sistema productivo son los entornos automatizados de producción debido a que permiten procesar un volumen alto de productos con un bajo margen de error.

La sima tecnológica de este tipo de sistema productivos son los sistemas CNC ya que permiten una completa automatización de los procesos de manufactura que requieren de cierta complejidad con relativa eficiencia con respecto a procesos manuales.

# Bibliografía

BCN. (2018). PIB-Enfoque de produccion. Managua: Banco Central de Nicaragua.

Hacienda. (Octubre de 2011). http://www.hacienda.gob.ni/presupuesto/informes/2011/. Obtenido de http://www.hacienda.gob.ni/documentos/presupuesto/informes/2011/INFORME%20EJECUCION%20PRESUPUESTARIA%20ENERO-SEPTIEMBRE%202011.pdf/view

Sepúlveda, A. (12 de Mayo de 2015). Nicaragua se suma a la impresión 3D. elnuevodiario.

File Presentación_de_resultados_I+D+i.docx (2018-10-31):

Diseño y fabricación de una máquina Control Numérico Computarizado (CNC) ROUTER de 3 ejes

Ariel Enoc Cisnero Rizo, Richard José Valverde Ramírez, Edwin Osmar Ruiz Mejía

UNI RUPAP Facultad de Tecnologías de la Industria (FTI)

ricvr98@gmail.com , arielcisnero95@gmail.com, civic2686@gmail.com

Resumen: Las máquinas de control numérico o CNC son el alma de la manufactura a gran escala por lo tanto decidimos hacer un esfuerzo en entender la tecnología con el fin de facilitar la comprensión de cómo y cuándo se deben utilizar, además de que planteamos una metodología de diseño mecánico la cual hemos ido refinando a lo largo de los proyectos en los que hemos trabajado dejando en esta investigación nuestras conclusiones de cómo se debe elaborar un producto en este caso un CNC siendo esta investigación un arma de doble filo en donde se plantean los medios(Manufactura en máquinas CNC) para llevar a cabo el fin(Producto) que se proponga. No está de más decir que se ha tratado de utilizar lo último en tendencias de diseño y que nuestro proyecto es open hardware el cual tiene como objetivo beneficiar a la mayor cantidad de gente directa o indirectamente.

Introducción: Personalmente la maquina la fabricamos debido a las dificultades que pasamos al fabricar otros proyectos anteriormente, así que decidimos diseñar y fabricar nuestra propia herramienta; en el camino logramos observar que este tipo de máquinas tienen una gran utilidad la cual se acentúa en un país como lo es Nicaragua principalmente porque la mayoría de lo que se exporta son materias primas y hacemos énfasis en esto debido a que una mayor presencia de los ingenieros en el campo de la manufactura aumentaría el dinero percibido por el país ya que los procesos de manufactura como los ofrecidos por los sistemas CNC’s aportan valor a los productos que se exporten. En corto plazo el objetivo del proyecto es ofrecer a la Facultad de Tecnologías de la Industria (FTI) una nueva herramienta con la cual hacer nuevos proyectos además de una metodología probada sobre cómo llevarlos a cabo; a largo plazo es sensibilizar a la comunidad en general de las ventajas que presenta la incorporación de la maquinaria CNC a los procesos artesanales con el fin de aumentar la calidad y el volumen de los productos procesados localmente.

Aplicación: Carreras como la ingeniería mecánica dependen de mucha practica para dotar de la experticia necesaria a los estudiantes que la cursan y actualmente la carrera de ingeniería mecánica y su facultad no cuenta con ninguna máquina para hacer prácticas de mecanizado de piezas en sistemas CNC por lo tanto podemos nombrar como una aplicación concreta al hecho de que al finalizar la investigación se contara con una maquina al servicio de los estudiantes que les permitirá ampliar sus conocimientos y sus fronteras a la hora de fabricar nuevos prototipos.

Beneficiarios: Estudiantes y docentes de la facultad de tecnología de la industria.

Metodología: La fabricación de piezas por arranque de viruta es un proceso en el que un cabezal giratorio que sostiene una broca(endmill) palpa una superficie hasta quitar la cantidad adecuada de material quedando finalmente una pieza con la geometría buscada. Este tipo de procesos llevan más de 100 años llevándose a cabo y desde que se comenzaron a implementar este tipo de maquinas la trayectoria del usillo se ha trazado de manera visual por los operarios requiriendo así de mano de obra capacitada con una gran pericia para la elaboración de las distintas partes que componen una máquina.

Desde el punto de vista matemático para automatizar el proceso de mecanizado mediante sistema CNC lo primero es definir el conjunto de geometrías que componen el sólido a mecanizar, afortunadamente programas CAD como solidworks, inventor o fusión 360 nos permiten representar una pieza de una manera fácil e intuitiva, además de facilitar la evaluación de las mismas en condiciones de trabajo a como se puede observar en la figura 1 en donde se presenta el diseño de una maquina la cual fue evaluada en solidworks reduciendo así la cantidad de iteraciones al momento de prototipar.

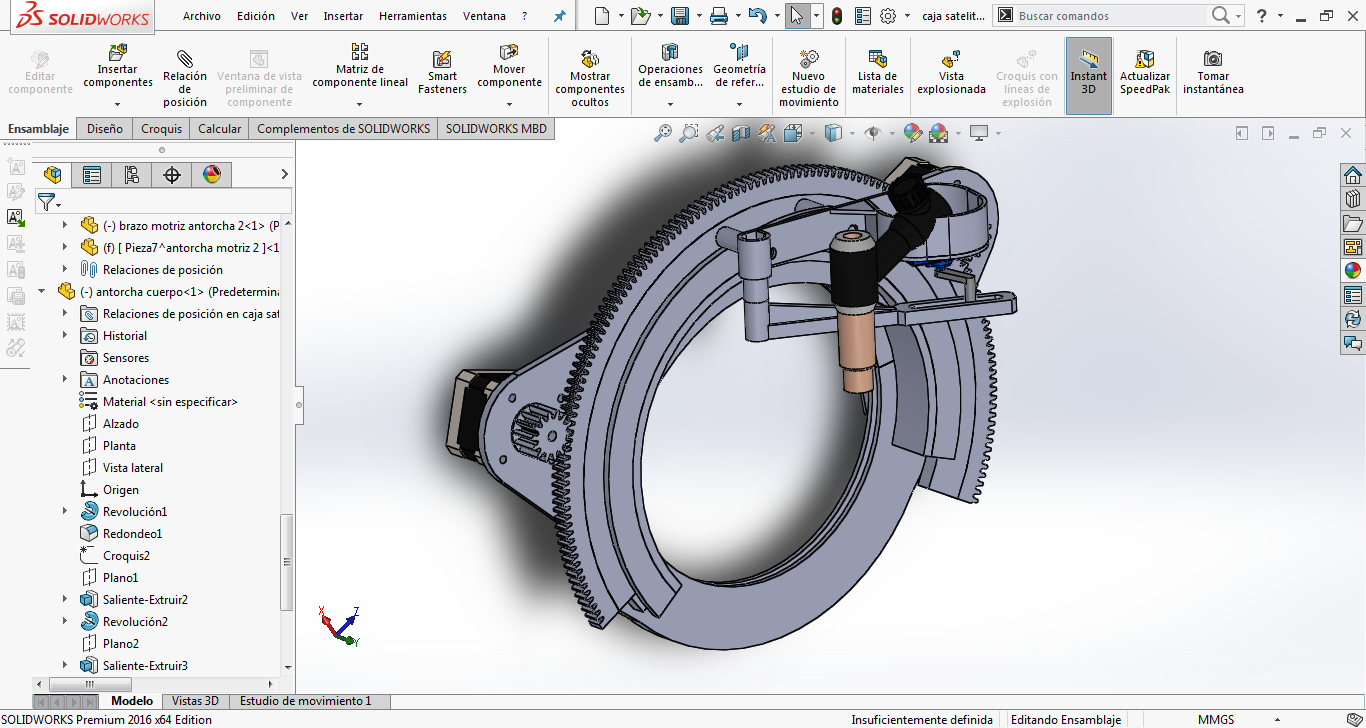
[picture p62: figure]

Figura 1 /Sistema CAD / Fuente propia

Una vez se ha definido la geometría de los componentes de la maquina se procede a la manufactura, en este punto cabe señalar que no todas las piezas se prestan a ser mecanizadas por lo tanto se ha de evaluar individualmente las piezas a fin de encontrar el proceso más adecuado para su fabricación. En el caso de que se halla elegido los procesos de arranque de viruta se sugiere optar por los procesos CNC sobre los procesos manuales por fines didácticos además de la mejora en la precisión que presentan estos procesos.

En este punto dentro de esta investigación se ha decidido utilizar fusión 360 como programa para generar las trayectorias a seguir por la maquina (como se observa en la figura 2) debido principalmente al apoyo que ofrecen a las entidades educativas y la gran cantidad de recursos que Autodesk destina a la formación de sus usuarios.

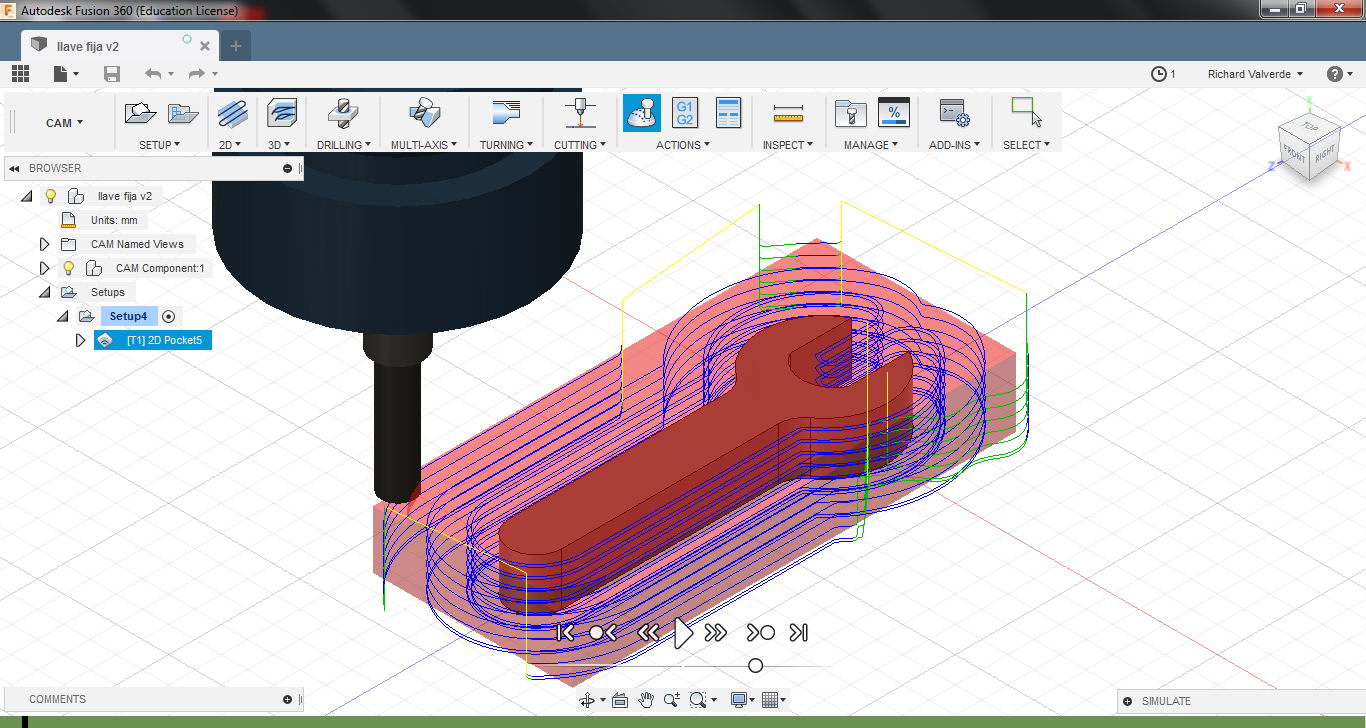
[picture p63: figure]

Figura 2/ Sistema CAM / Fuente propia

Finalmente, el programa CAM (fusión 360) exporta un archivo que es legible por la maquina CNC la que se encarga de materializar la pieza de forma autónoma como se puede observar en la figura 3.


Figura 3/ Mecanizado en CNC / Fuente propia

Resultados: Siendo honestos este proyecto no habría sido posible sin el conocimiento adquirido en otros cuatro proyectos anteriormente realizados por lo tanto debo afirmar que uno de los resultados más importantes obtenidos en esta investigación es la metodología para desarrollar un proyecto(producto) exitosamente y he de decir esto ya que no todos los proyectos que se realizaron anteriormente fueron exitosos aun así marcaron un precedente sobre el cual se presenta este proyecto.


Figura 4/ Diseño CAD vs Maquina real / Fuente propia

A como se puede observar en la figura 4 logramos ejecutar el diseño al pie de la letra logrando los resultados deseados producto de la metodología de diseño y manufactura. Hay que recalcar que el diseño mecánico de esta máquina es enteramente realizado por nosotros y desarrollamos un conjunto de cálculos de soporte para optimizar la elección y calibración de los motores en función a las fuerzas que actúen sobre cada eje. Esta máquina a como se observa en la figura 4 está en la primera iteración actualmente se encuentra en la segunda iteración la cual tiene como fin aumentar su rendimiento y fiabilidad.

Por último pero no menos importante esta la administración y control de versión del proyecto, el cual se llevó en GitHub a como se observa en la figura 5 con el objetivo de que el proyecto esté al alcance de cualquiera.

Link: https://github.com/Ricvr98/CNC-UNI-Monografia-

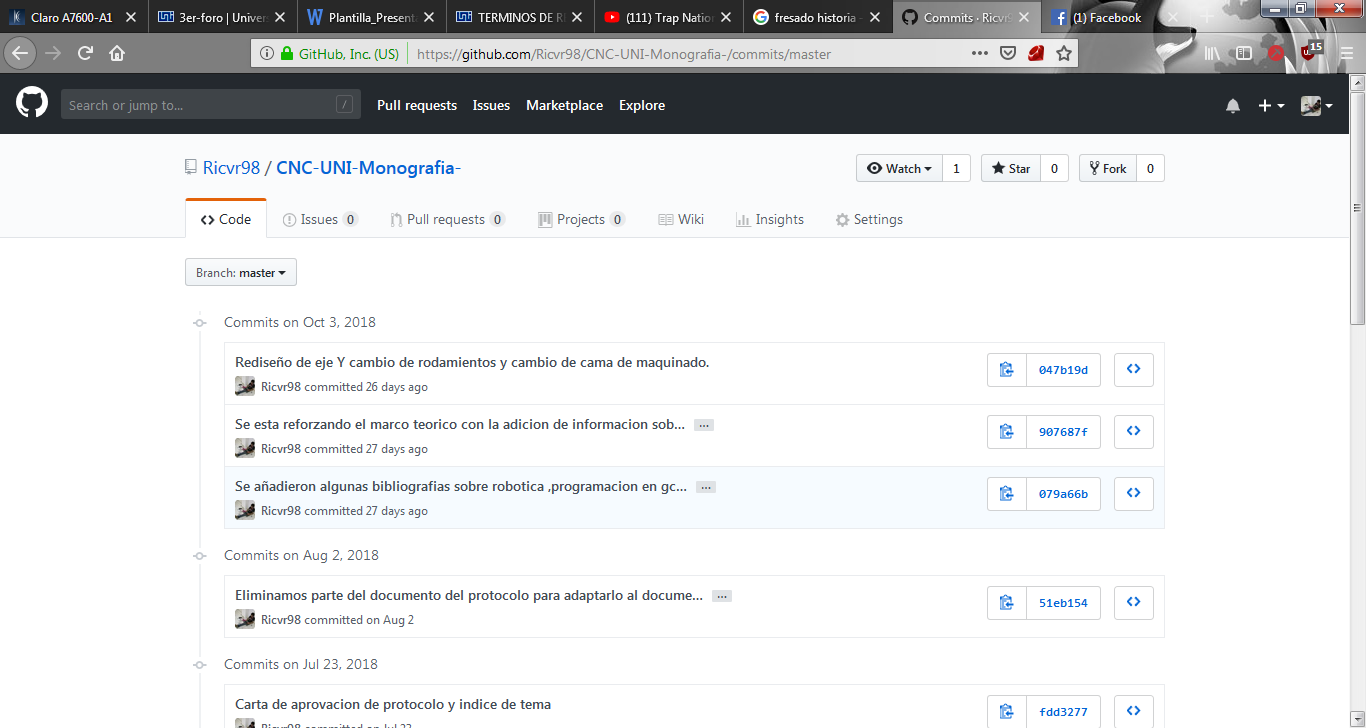
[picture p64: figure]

Figura 5/ Git-Hub /Fuente propia

Perspectivas futuras: Aspiramos a que la investigación sirva como base para nuevos proyectos en pro de la comunidad universitaria más específicamente se podrían desarrollar derivados de esta tecnología tales como las cortadoras de plasma, impresoras 3D y escáneres 3D que potenciarían aún más el alcance de este proyecto.

Productos de Investigación: A partir de esta investigación se ha podido desarrollar la tesis de pregrado “Diseño y fabricación de una máquina Control Numérico Computarizado (CNC) ROUTER de 3 ejes para el taller de Máquinas Herramientas de la Facultad de Tecnología de la Industria en la Universidad Nacional de Ingeniería (UNI-RUPAP)” en la facultad de tecnología de la industria la cual todavía está en desarrollo.

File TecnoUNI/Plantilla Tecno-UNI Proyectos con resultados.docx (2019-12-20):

Manufactura en maquinaria CNC aplicada a proyectos académicos y posibles usos en la industria local

“Ariel Enoc Cisnero Rizo”, “Richard José Valverde Ramírez”, “Mary Triny Gutiérrez Mendoza”

Ariel Enoc Cisnero Rizo---------------------------------------------------------------- FTI

Richard José Valverde Ramírez------------------------------------------------------ FTI

Mary Triny Gutiérrez Mendoza ----------------------------------------------------- FTI

arielcisnero95@gmail.com, ricvr98@gmail.com, gtrini15@yahoo.es

Introducción: Las máquinas de control numérico o CNC son el alma de la manufactura a gran escala por lo tanto decidimos hacer un esfuerzo en entender la tecnología con el fin de facilitar la comprensión de cómo y cuándo se deben utilizar, además de que planteamos una metodología de diseño mecánico la cual hemos ido refinando a lo largo de los proyectos en los que hemos trabajado dejando en esta investigación nuestras conclusiones de cómo se debe elaborar un producto siendo esta investigación un arma de doble filo en donde se plantean los medios(Manufactura en máquinas CNC) para llevar a cabo el fin(Producto) que se proponga además se ha tratado de utilizar lo último en tendencias de diseño y que nuestro proyecto es open hardware el cual tiene como objetivo beneficiar a la mayor cantidad de gente directa o indirectamente.

En el transcurso de este proyecto se utilizó una maquina (CNC router de tres ejes) desarrollada como monografía por los autores de esta investigación para llevar a cabo un proyecto (mecanismo Theo Jansen) el cual consiste en la fabricación de los componentes de esta máquina con la ventaja de que dicho mecanismo (Theo jansen) ya se había fabricado de manera artesanal anteriormente por nosotros mismos permitiéndonos así comparar los métodos de manufactura utilizados en los respectivos prototipos (artesanal/automatizado) con el objetivo de argumentar sobre las ventajas que presentan los CNC’s como proceso de manufactura y en qué circunstancias su uso es adecuado, no está de más decir que el campo de aplicación de esta investigación abarca tanto el académico como el industrial/comercial.

Aplicación y Beneficiarios: Actualmente a raíz del proyecto investigativo y monografía (CNC router de tres ejes) se ha dotado a la universidad de la herramienta adecuada para desarrollar las habilidades de los estudiantes de la comunidad universitaria en proyectos de mayor complejidad., es decir parte de los resultados que se buscan es demostrar las capacidades de este tipo de maquina (Maquinas CNC en general) cuando se usan con la metodología adecuada en proyectos multidisciplinarios.

Con el objetivo de verificar las mejoras en los procesos de manufactura se espera comparar dimensionalmente las piezas realizadas y obtener pruebas experimentales que avalen nuestros objetivos.

Acorde a los resultados de las pruebas se definirán los tipos de productos locales que podrían tener una mejora sustancial en términos de calidad y rentabilidad.

Inicialmente el conjunto de máquina y metodología plantea ser un proyecto demostrativo con el único y simple objetivo de incentivar a la comunidad universitaria a generar propuestas de soluciones a problemas en la manera de productos. Principalmente la metodología de manufactura está enfocada al perfil de la ingeniería mecánica, pero hacemos énfasis que para un correcto funcionamiento es necesario crear equipos multidisciplinarios para generar una propuesta conjunta según el caso lo requiera.

Finalmente esperamos que como resultado estos proyectos mejoren de una u otra manera la calidad de vida de la población en general basándonos en que la generación de nuevos productos como solución de problemas le permite a la industria local ser más competitiva y a la vez la población en general pueda obtener mejores trabajos.

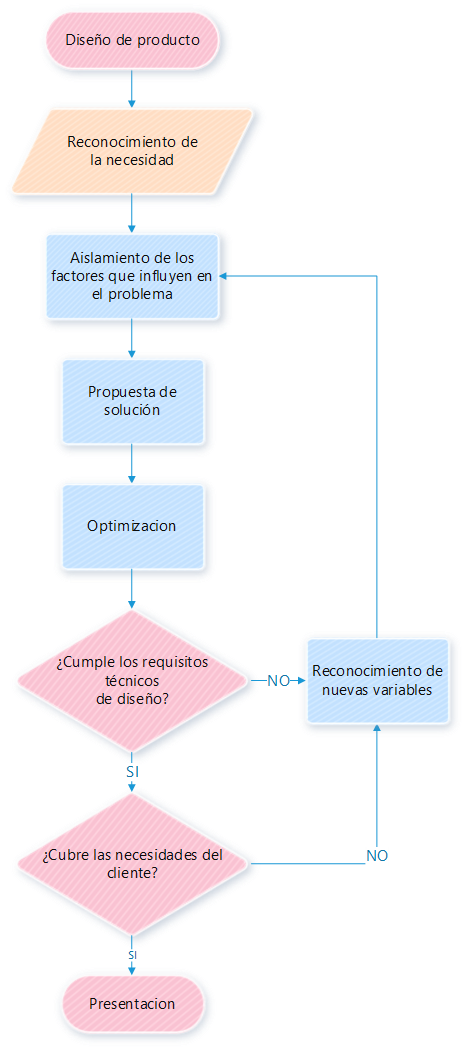
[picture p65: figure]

Metodología: Esta investigación es la continuación de un proyecto investigativo previamente elaborado por nosotros el cual se titulaba “Diseño y fabricación de una máquina Control Numérico Computarizado (CNC) ROUTER de 3 ejes” y por lo tanto se trabajara sobre lo desarrollado en aquel proyecto con el objetivo de ampliar el alcance de la investigaciones como un conjunto.

Diseño

“Se podría definir la actividad creativa como un tipo de proceso de aprendizaje en el que el profesor y el alumno se hallan en el mismo individuo.”

― Arthur Koestler

El diseño mecánico es como cualquier proceso creativo en el cual se intenta recrear lo que en este caso la mente percibe como una solución. Según la frase de Arthur Koestler, se puede reflexionar sobre la misma, la complejidad del proceso de diseño en un entorno tan competitivo como el que existe actualmente es necesario formular nuevas máquinas (como solución) cada vez más eficientes, teniendo así el diseñador la tarea de empujar los límites de lo que se cree posible confirmando así que muchas veces el profesor y el alumno se encuentran en el mismo individuo.

Parte del objetivo de este proyecto consiste en saber cómo abordar un problema a fin de poder sintetizar una solución no solo eficaz sino competitiva, por lo tanto, muchas veces se tendrá que pensar fuera de la caja para eludir las dificultades que el problema plantee, teniendo así inevitablemente que innovar en el producto que se plantee con el objetivo de competir en el mercado con nuestra oferta.

En el diagrama de flujo que se observa en la imagen, se plantea un proceso simple pero genérico para enfrentar el proceso de diseño.

Este diagrama de flujo es resultado de varios proyectos que se han ejecutado. En este se plantean unas series de conclusiones acerca de cuál es el orden de actividades a seguir a fin de crear un diseño que cumpla las necesidades planteadas en la menor cantidad de iteraciones posibles.

Manufactura

El diseño es solo filosofía sin una manufactura que la respalde, es importante recalcar que al momento de diseñar se tiene que tener en cuenta las materias primas con las que se cuenta localmente y de los procesos de manufactura que se les puede aplicar a las materias primas con las maquinas que se tienen a disposición.

En este caso se optimizo el diseño en la medida de que fuese viable fabricar la mayor cantidad de piezas posibles en el proceso de fresado de tres ejes. A partir del diseño se logró concluir en la tabla siguiente los procesos de manufactura necesarios para fabricar el mecanismo propuesto.

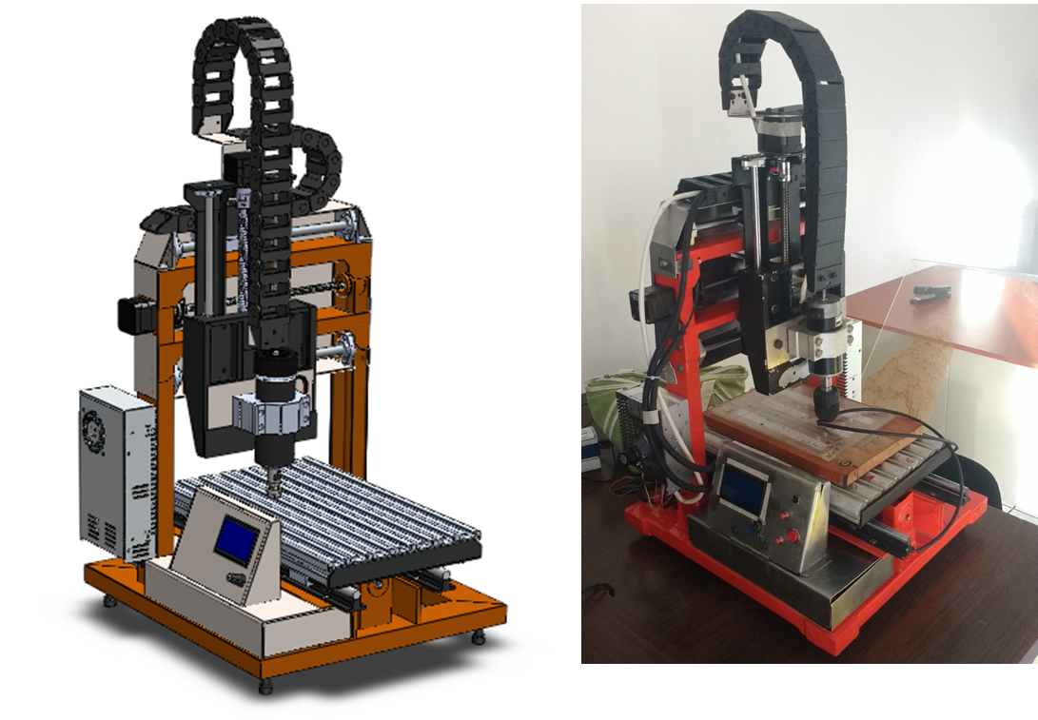
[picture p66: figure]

Describir los métodos y materiales (softwares, equipos, instrumentos, etc.) implementados. Incluya las figuras que crea pertinente, enumérelas y póngales su título debajo de la figura anteponiendo la etiqueta “Figura X”, por ejemplo la Figura 1. De igual forma incluya las tablas que crea pertinente, enumérelas y póngales su título encima de la tabla anteponiendo la etiqueta “Tabla X”, por ejemplo la Tabla 1.

Figura 1. Robot manipulador propuesto. (a) Vista general. (b) i-ésima cadena cinemática.

Tabla 1. Valores de referencia para los parámetros geométricos del robot.

Parámetro | Valor | Parámetro | Valor
Rf | 50 mm | r | 50 mm
Rr | 150 mm | θ1 | 35°
R2 | 450 mm | θ2 | 155°
Ho | 200 mm | θ3 | 275°
LA | 200 mm | θ4 | 25°
LB | 400 mm | θ5 | 145°
h | 34 mm | θ6 | 265°

Resultados: Detallar los principales resultados y hallazgos de la investigación. Incluya las figuras que crea pertinente, enumérelas y póngales su título debajo de la figura anteponiendo la etiqueta “Figura X”, por ejemplo la Figura 1. De igual forma incluya las tablas que crea pertinente, enumérelas y póngales su título encima de la tabla anteponiendo la etiqueta “Tabla X”, por ejemplo la Tabla 1.

Perspectivas futuras: Reflexionar sobre procesos posteriores relacionados a ampliar los resultados obtenidos.

NOTA: no superar dos páginas (borrar esta nota)

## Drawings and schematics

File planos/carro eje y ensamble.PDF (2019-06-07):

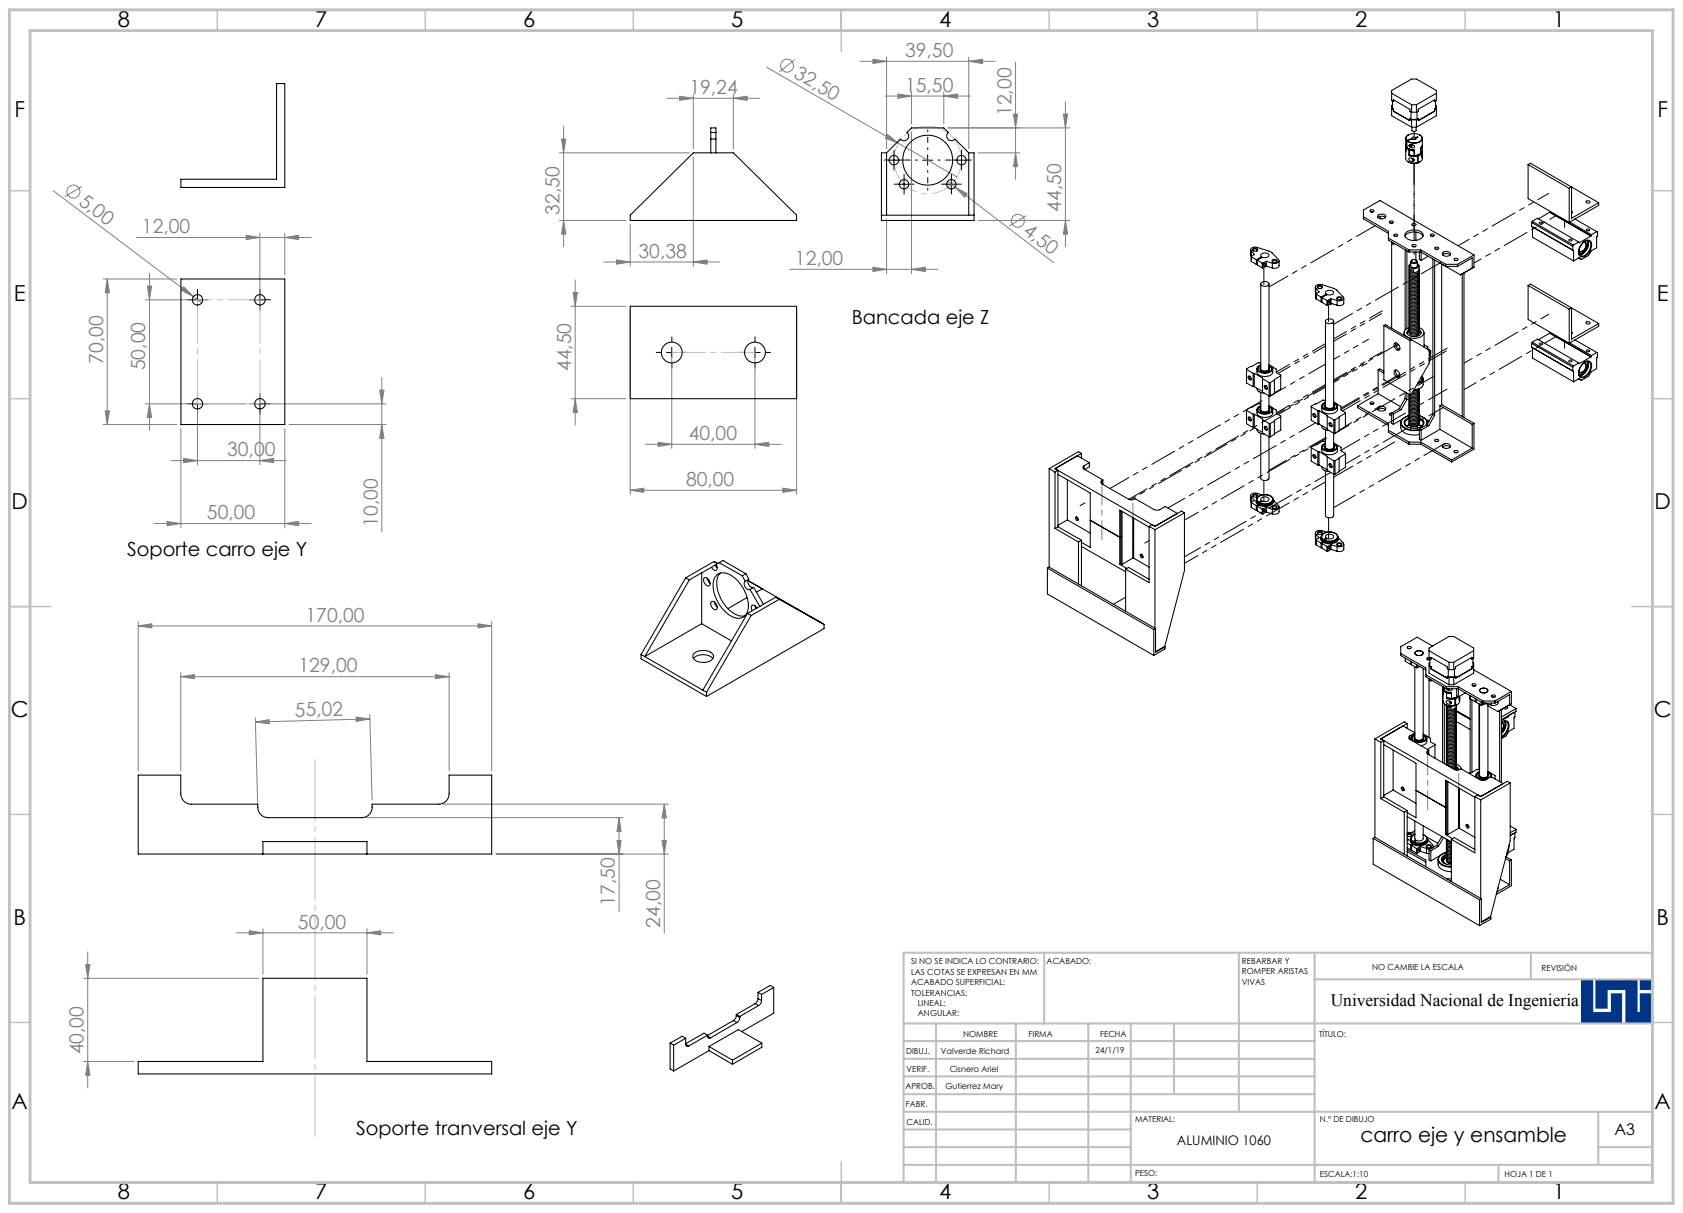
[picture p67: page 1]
Bancada eje Z; ACABADO:; REBARBAR Y; ROMPER ARISTAS; NO CAMBIE LA ESCALA; REVISIÓN; ESCALA:1:10; HOJA 1 DE 1

Soporte carro eje Y

SI NO SE INDICA LO CONTRARIO:
LAS COTAS SE EXPRESAN EN MM
ACABADO SUPERFICIAL:
TOLERANCIAS:
LINEAL:
ANGULAR:

Universidad Nacional de Ingenieria

NOMBRE | FIRMA | FECHA | | | | TÍTULO:

DIBUJ. | Valverde Richard | | 24/1/19
VERIF. | Cisnero Ariel
APROB. | Gutierrez Mary
FABR.
CALID. | | | | MATERIAL: | N.º DE DIBUJO carro eje y ensamble | A3 ALUMINIO 1060

Soporte tranversal eje Y

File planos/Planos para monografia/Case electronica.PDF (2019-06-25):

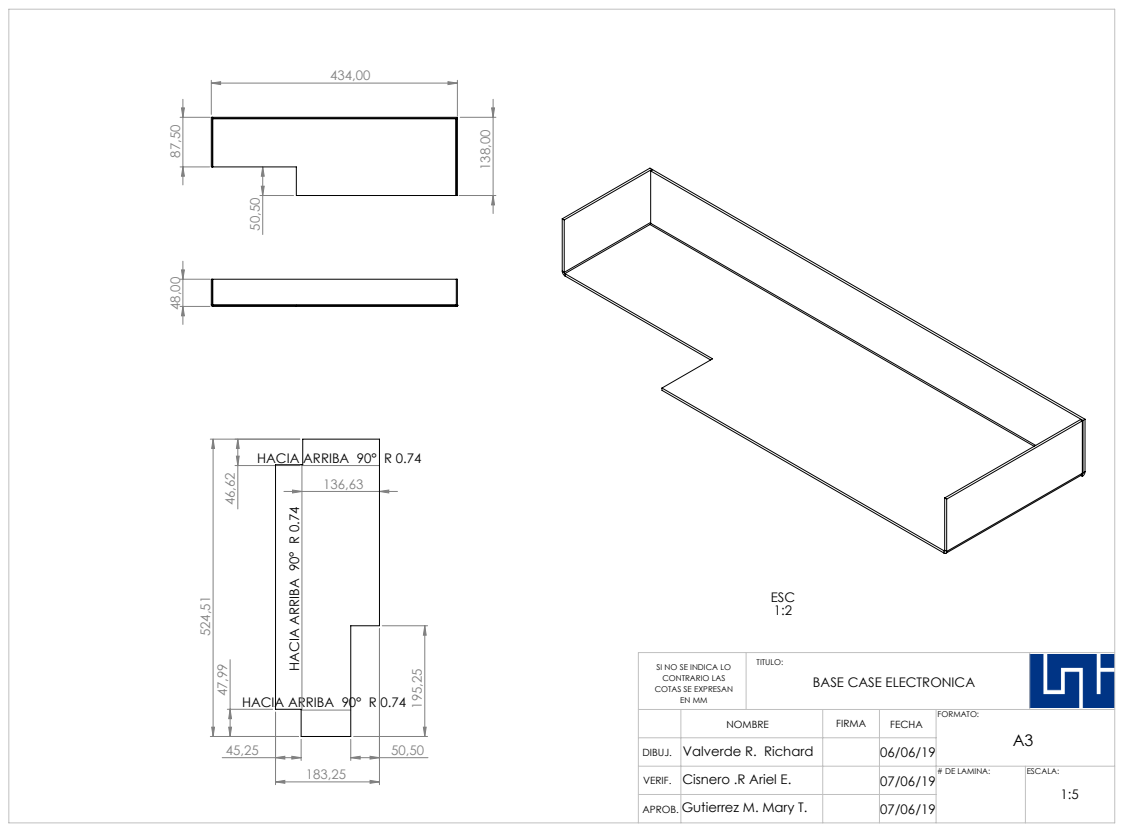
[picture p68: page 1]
HACIA ARRIBA 90°; R 0.74 HACIA ARRIBA 90° R 0.74; HACIA ARRIBA 90° R 0.74; Valverde R. Richard

SI NO SE INDICA LO CONTRARIO LAS COTAS SE EXPRESAN EN MM | TITULO: BASE CASE ELECTRONICA

NOMBRE | FIRMA | FECHA | FORMATO: A3

VERIF. | Cisnero .R Ariel E. | # DE LAMINA: | ESCALA:

APROB. | Gutierrez M. Mary T.

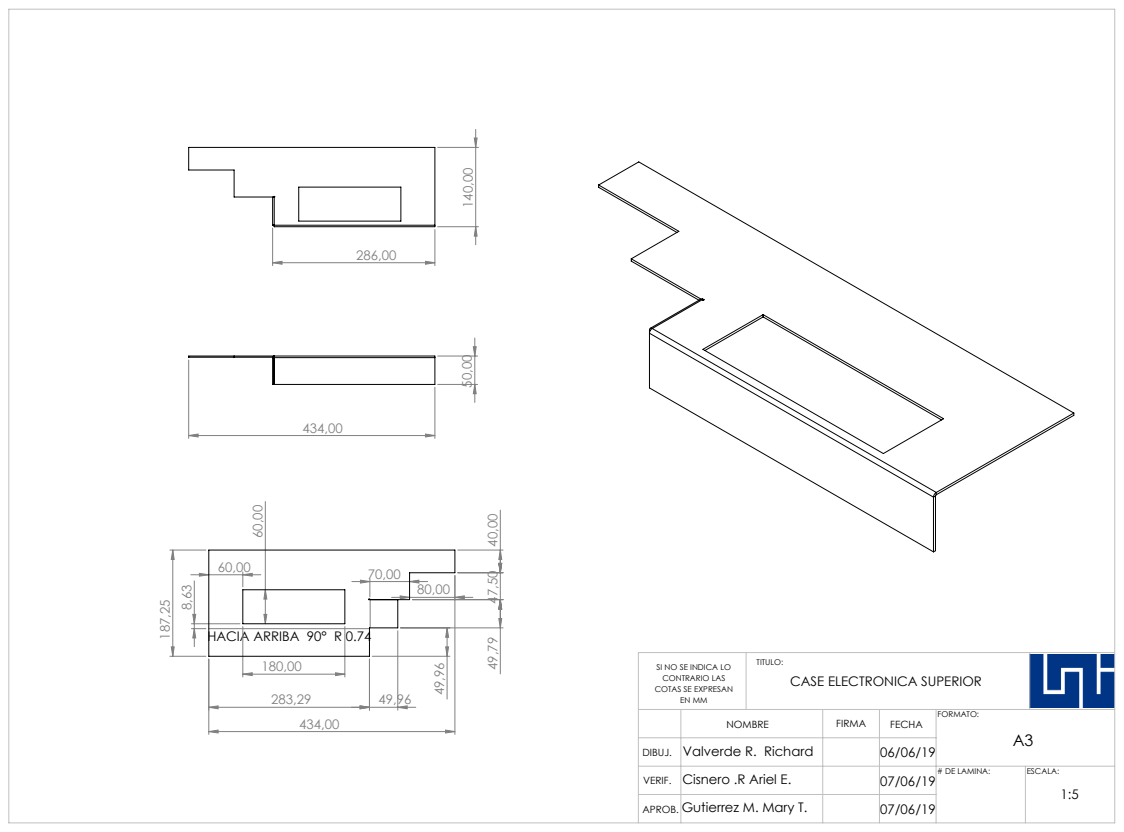
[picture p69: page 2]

HACIA ARRIBA 90° R 0.74

SI NO SE INDICA LO CONTRARIO LAS COTAS SE EXPRESAN EN MM | TITULO: CASE ELECTRONICA SUPERIOR

NOMBRE | FIRMA | FECHA | FORMATO: A3

DIBUJ. | Valverde R. Richard | | 06/06/19

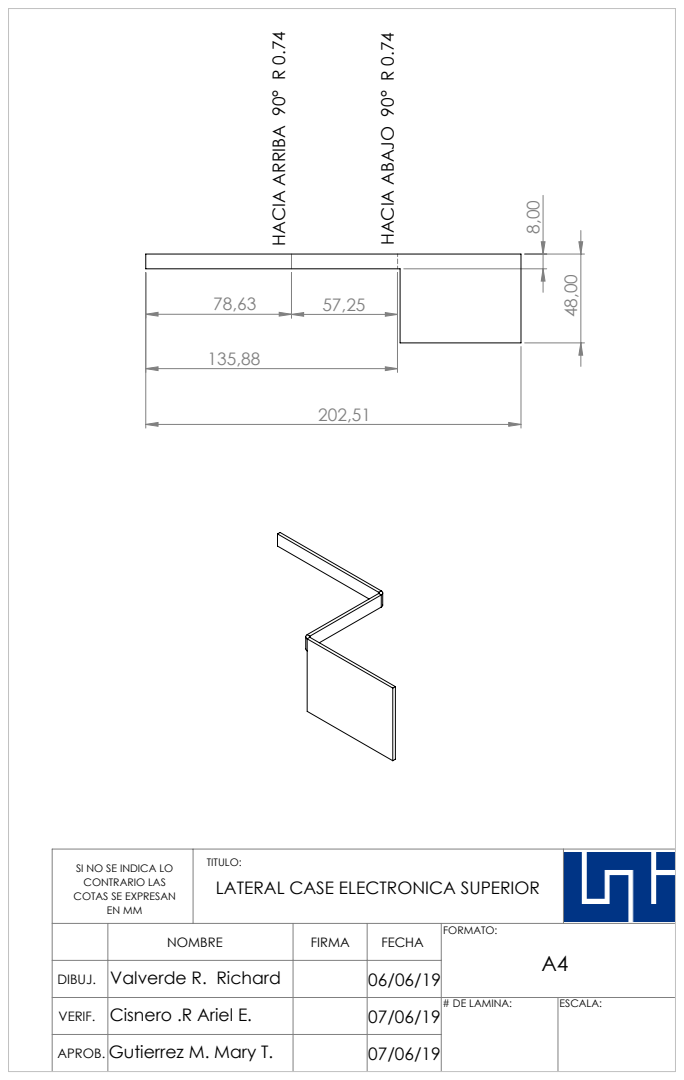
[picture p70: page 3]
HACIA ARRIBA 90° R 0.74; HACIA ABAJO 90° R 0.74

SI NO SE INDICA LO CONTRARIO LAS COTAS SE EXPRESAN EN MM | TITULO: LATERAL CASE ELECTRONICA SUPERIOR

NOMBRE | FIRMA | FECHA | FORMATO: A4

DIBUJ. | Valverde R. Richard | | 06/06/19

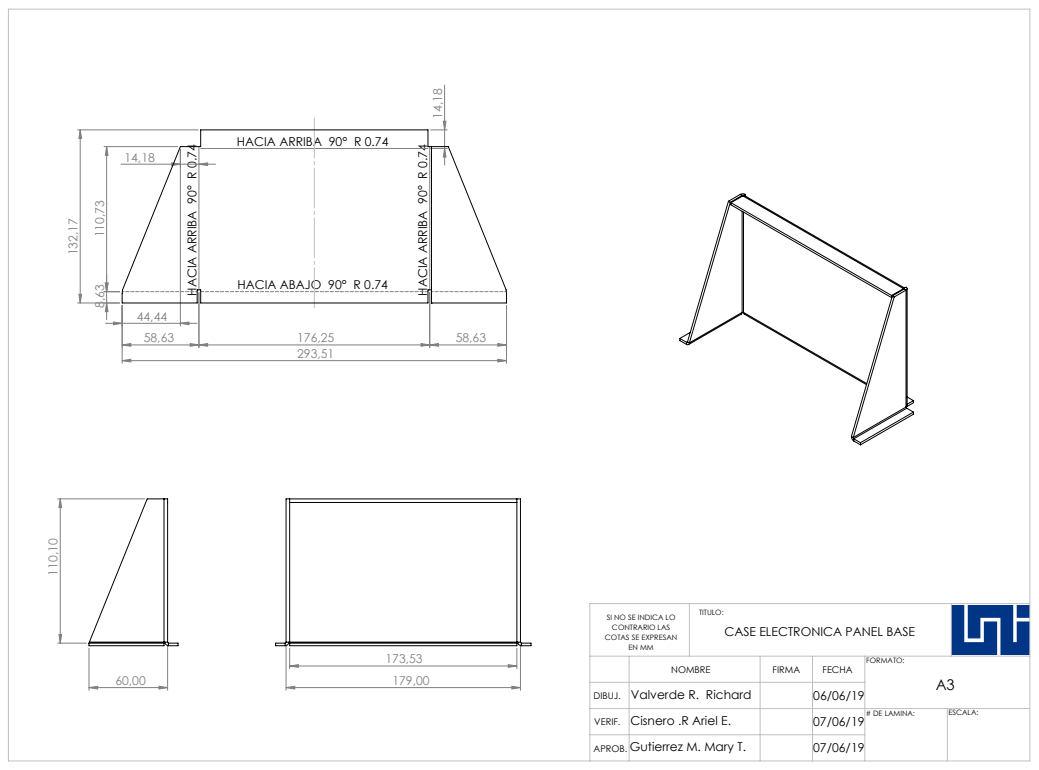
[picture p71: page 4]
HACIA ABAJO 90° R 0.74; HACIA ARRIBA 90° R 0.74

SI NO SE INDICA LO CONTRARIO LAS COTAS SE EXPRESAN EN MM | TITULO: CASE ELECTRONICA PANEL BASE

NOMBRE | FIRMA | FECHA | FORMATO: A3

DIBUJ. | Valverde R. Richard | | 06/06/19

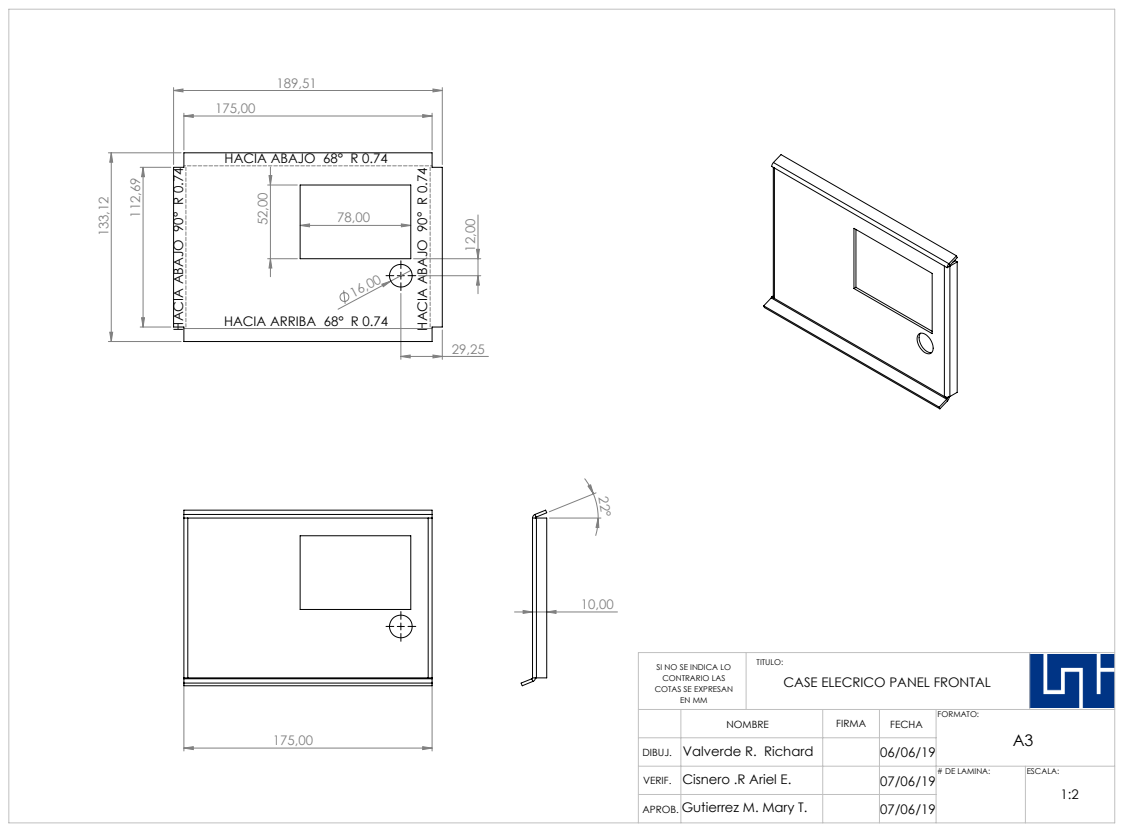
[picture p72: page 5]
HACIA ABAJO 90° R 0.74; HACIA ARRIBA 68° R 0.74; HACIA ABAJO 68° R 0.74

SI NO SE INDICA LO CONTRARIO LAS COTAS SE EXPRESAN EN MM | TITULO: CASE ELECRICO PANEL FRONTAL

NOMBRE | FIRMA | FECHA | FORMATO: A3

DIBUJ. | Valverde R. Richard | | 06/06/19

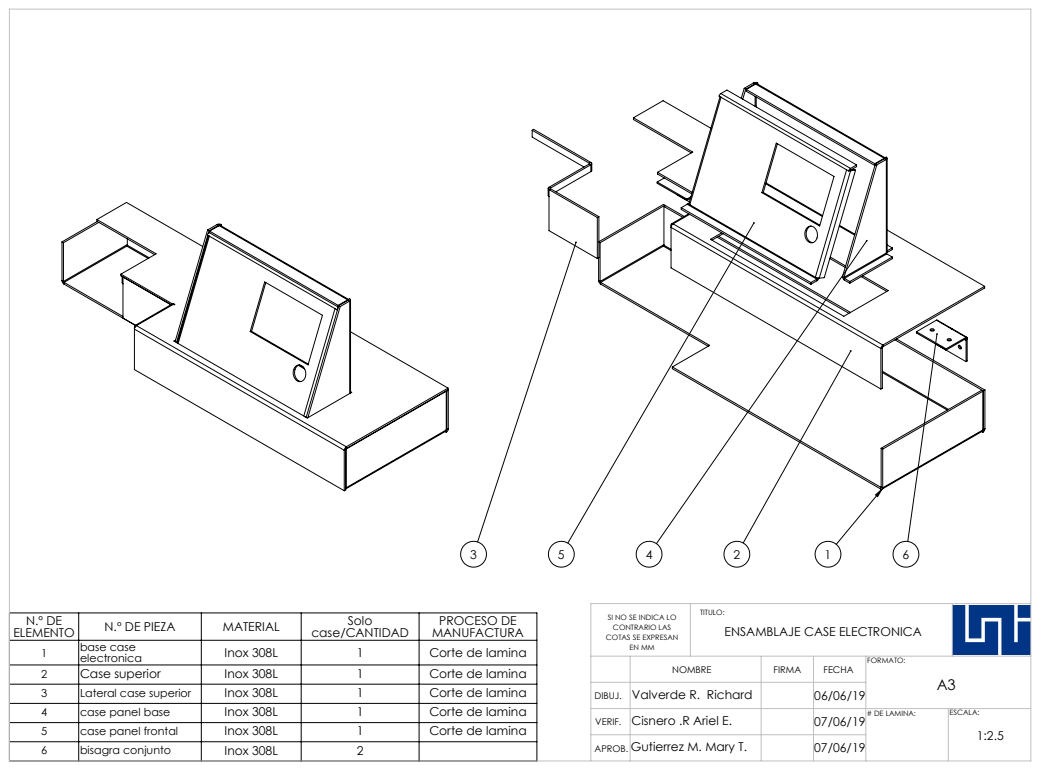
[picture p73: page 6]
Lateral case superior; Inox 308L; Corte de lamina; Valverde R. Richard

ELEMENTO N.º DE | N.º DE PIEZA | MATERIAL | Solo case/CANTIDAD | PROCESO DE MANUFACTURA
1 | base case electronica | Inox 308L | 1 | Corte de lamina
2 | Case superior | Inox 308L | 1 | Corte de lamina

SI NO SE INDICA LO CONTRARIO LAS COTAS SE EXPRESAN EN MM | TITULO: ENSAMBLAJE CASE ELECTRONICA

NOMBRE | FIRMA | FECHA | FORMATO: A3

4 | case panel base | Inox 308L | 1 | Corte de lamina
5 | case panel frontal | Inox 308L | 1 | Corte de lamina
6 | bisagra conjunto | Inox 308L | 2

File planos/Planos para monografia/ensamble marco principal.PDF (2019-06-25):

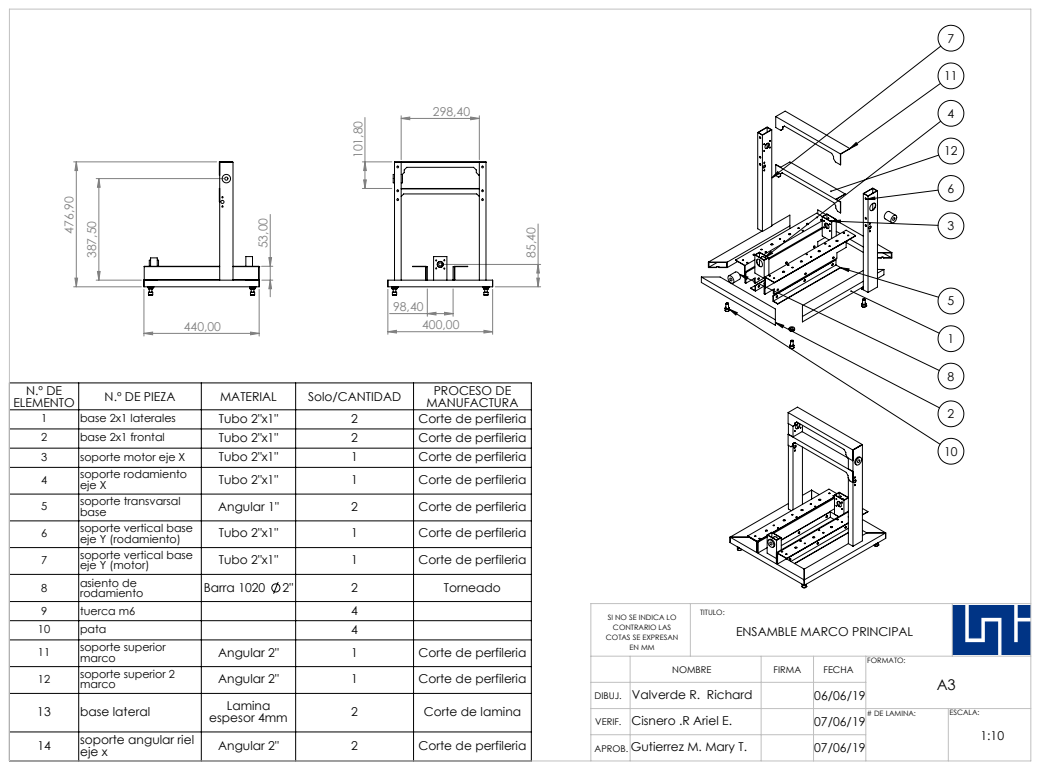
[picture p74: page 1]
tuerca m6

ELEMENTO N.º DE | N.º DE PIEZA | MATERIAL | Solo/CANTIDAD | PROCESO DE MANUFACTURA
1 | base 2x1 laterales | Tubo 2"x1" | 2 | Corte de perfileria
2 | base 2x1 frontal | Tubo 2"x1" | 2 | Corte de perfileria
3 | soporte motor eje X | Tubo 2"x1" | 1 | Corte de perfileria
4 | soporte rodamiento eje X | Tubo 2"x1" | 1 | Corte de perfileria
5 | soporte transvarsal base | Angular 1" | 2 | Corte de perfileria
6 | soporte vertical base eje Y (rodamiento) | Tubo 2"x1" | 1 | Corte de perfileria
7 | soporte vertical base eje Y (motor) | Tubo 2"x1" | 1 | Corte de perfileria
8 | asiento de rodamiento | Barra 1020 2" | 2 | Torneado

SI NO SE INDICA LO
CONTRARIO LAS
COTAS SE EXPRESAN

TITULO:
ENSAMBLE MARCO PRINCIPAL

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

NOMBRE | FIRMA | FECHA | FORMATO: A3

DIBUJ. | Valverde R. Richard | | 06/06/19
VERIF. | Cisnero .R Ariel E. | | 07/06/19 | # DE LAMINA: | ESCALA: 1:10

14 | soporte angular riel eje x | Angular 2" | 2 | Corte de perfileria

APROB. | Gutierrez M. Mary T. | | 07/06/19

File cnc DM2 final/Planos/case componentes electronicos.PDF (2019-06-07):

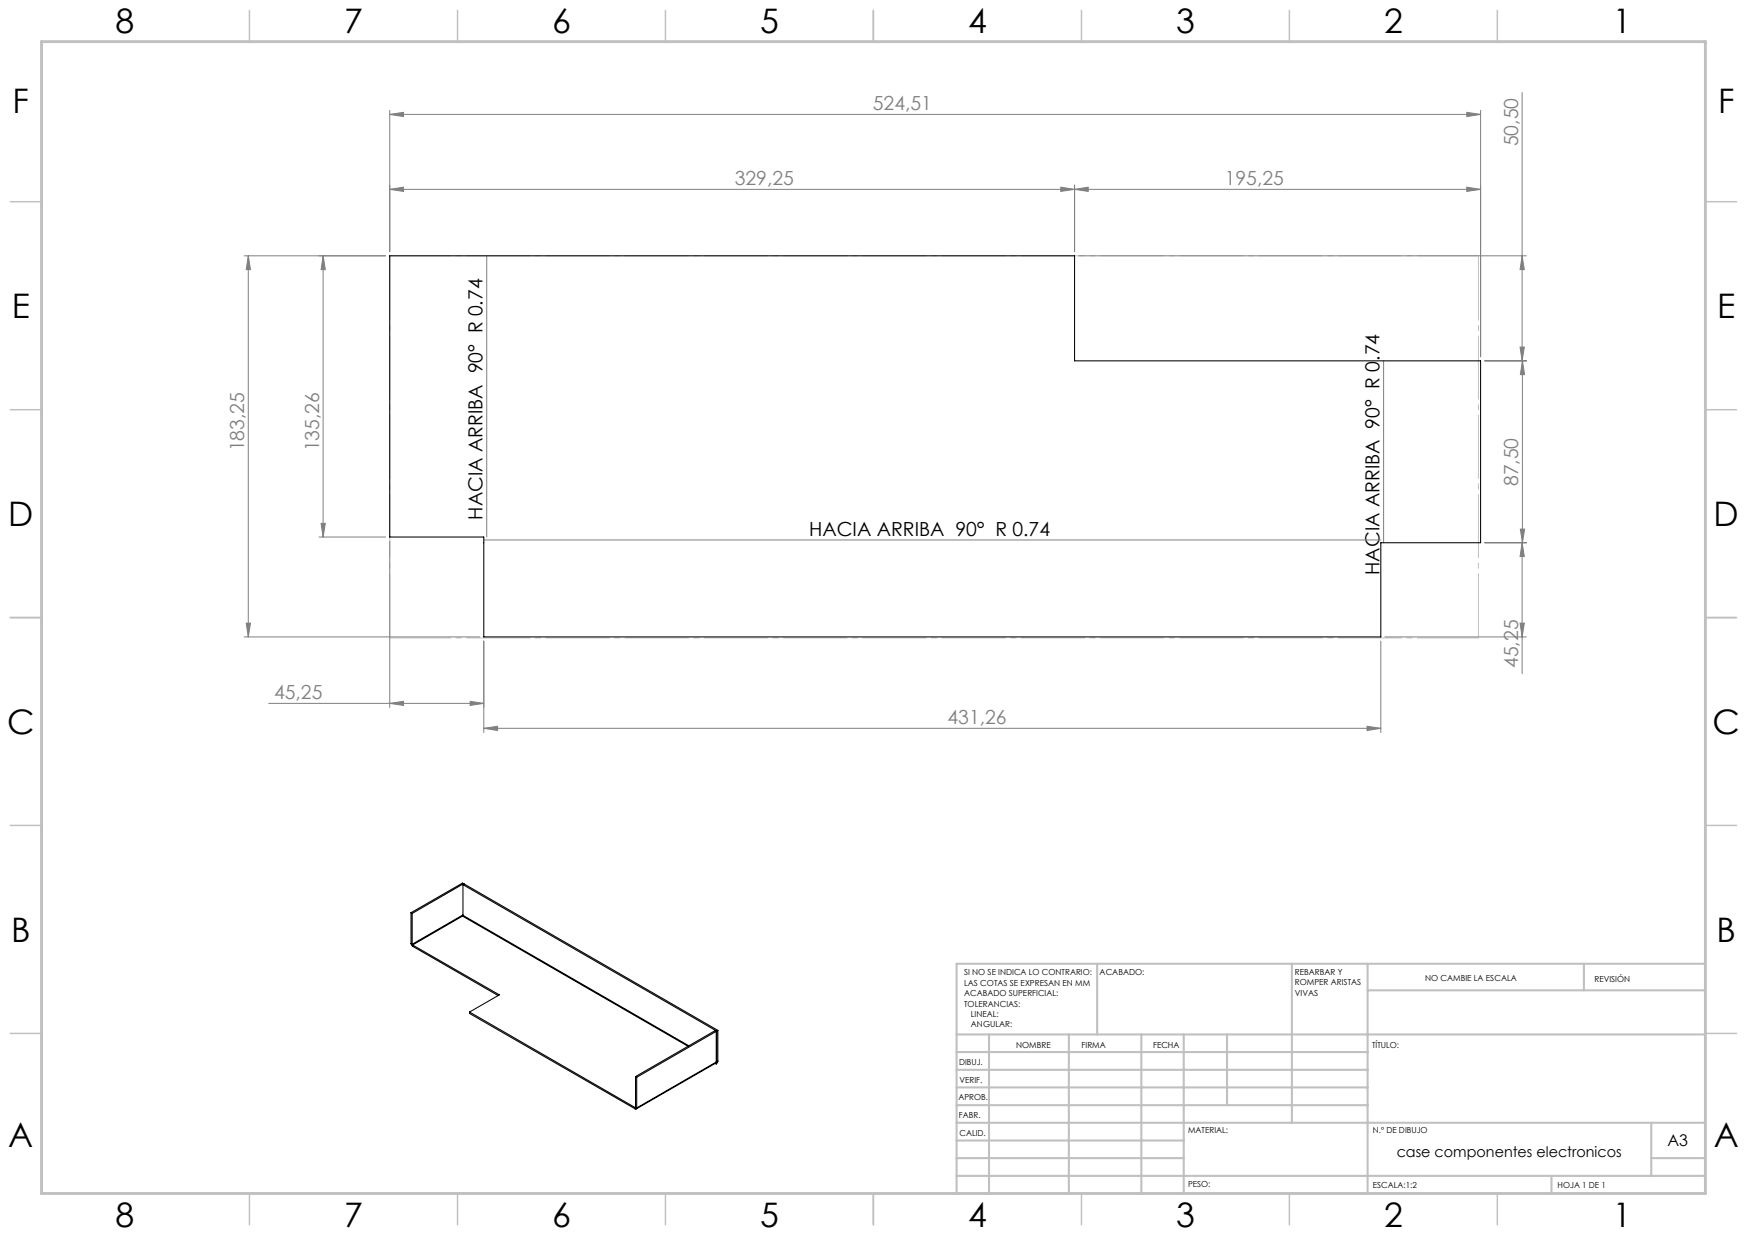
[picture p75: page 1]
HACIA ARRIBA 90° R 0.74; ACABADO:; REBARBAR Y; ROMPER ARISTAS; NO CAMBIE LA ESCALA; REVISIÓN; ESCALA:1:2; HOJA 1 DE 1; case componentes electronicos

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

NOMBRE | FIRMA | FECHA | | | | TÍTULO:

DIBUJ.
VERIF.
APROB.
FABR.
CALID. | | | | MATERIAL: | N.º DE DIBUJO | A3

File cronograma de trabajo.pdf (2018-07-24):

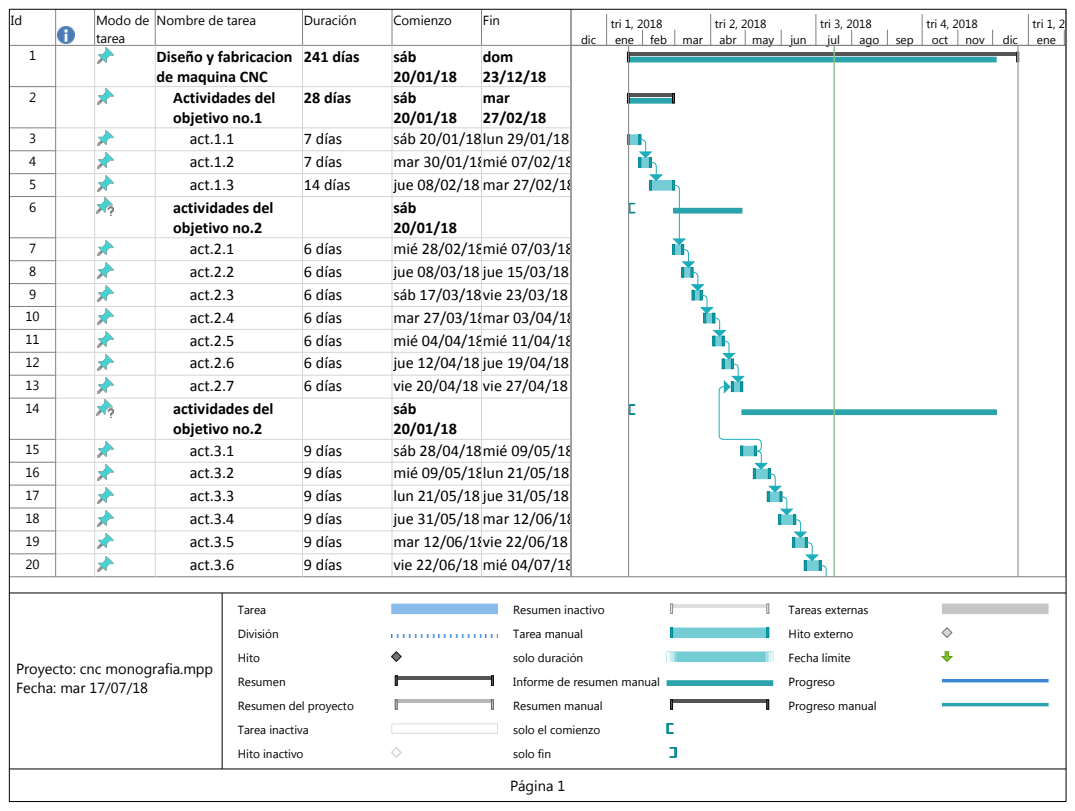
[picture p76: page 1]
Modo de; tarea; Nombre de tarea; Duración; Comienzo; Fin; Diseño y fabricacion; 241 días; sáb; dom 23/12/18; Actividades del; objetivo no.1; 28 días; mar 27/02/18; act.1.1; 7 días; sáb 20/01/18lun 29/01/18; act.1.2; mar 30/01/18mié 07/02/18; act.1.3; 14 días; jue 08/02/18 mar 27/02/18; actividades del; objetivo no.2; sáb 20/01/18; act.2.1; 6 días; mié 28/02/18mié 07/03/18; act.2.2; jue 08/03/18 jue 15/03/18; act.2.3; sáb 17/03/18vie 23/03/18; act.2.4; mar 27/03/18mar 03/04/18; act.2.5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

de maquina CNC

Proyecto: cnc monografia.mpp
Fecha: mar 17/07/18

Informe de resumen manual

Resumen del proyecto

solo el comienzo

Id | Modo de
tarea
Nombre de tarea | Duración | Comienzo | Fin
21 | act.3.7 | 9 días | mié 04/07/18lun 16/07/18
22 | act.3.8 | 9 días | lun 16/07/18 jue 26/07/18
23 | act.3.9 | 9 días | jue 26/07/18 mar 07/08/18
24 | act.3.10 | 9 días | mar 07/08/18vie 17/08/18
25 | act.3.11 | 9 días | vie 17/08/18 mié 29/08/18
26 | act.3.12 | 9 días | mié 29/08/18lun 10/09/18
27 | act.3.13 | 9 días | lun 10/09/18 jue 20/09/18
28 | act.3.14 | 9 días | jue 20/09/18 mar 02/10/18
29 | act.3.15 | 9 días | mar 02/10/18vie 12/10/18
30 | act.3.16 | 9 días | vie 12/10/18 mié 24/10/18
31 | act.3.17 | 15 días | mié 24/10/18mar 13/11/18
32 | act.3.18 | 15 días | mar 13/11/18lun 03/12/18
dic | ene | feb | mar | abr | may | jun | jul | ago | sep | oct | nov | dic | ene
tri 1, 2018 | tri 2, 2018 | tri 3, 2018 | tri 4, 2018 | tri 1, 2019

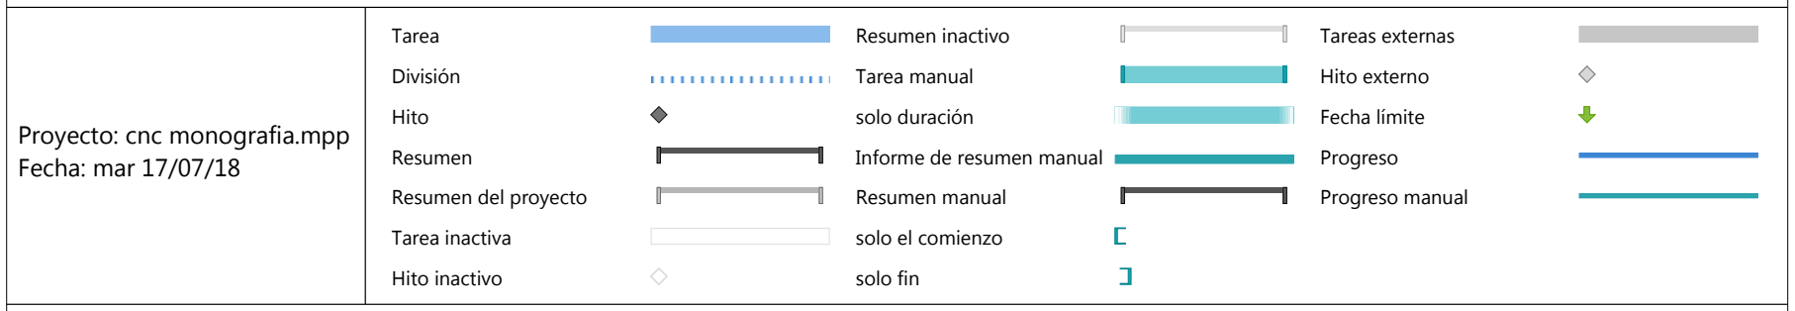
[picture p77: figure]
Tarea; División; Hito; Resumen; Resumen del proyecto; Tarea inactiva; Hito inactivo; Resumen inactivo; Tarea manual; solo duración; Informe de resumen manual; Resumen manual; solo el comienzo; solo fin; Tareas externas; Hito externo; Fecha límite; Progreso; Progreso manual; Proyecto: cnc monografia.mpp Fecha: mar 17/07/18

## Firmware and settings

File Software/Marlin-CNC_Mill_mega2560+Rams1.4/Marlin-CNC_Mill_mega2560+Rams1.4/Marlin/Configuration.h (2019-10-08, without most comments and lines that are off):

#define CONFIGURATION_H
#define CONFIGURATION_H_VERSION 010100
#define STRING_CONFIG_H_AUTHOR "(none, default config)" // Who made the changes.
#define SHOW_BOOTSCREEN
#define STRING_SPLASH_LINE1 SHORT_BUILD_VERSION // will be shown during bootup in line 1
#define STRING_SPLASH_LINE2 WEBSITE_URL         // will be shown during bootup in line 2
#define SHOW_CUSTOM_BOOTSCREEN
#define SERIAL_PORT 0
#define BAUDRATE 115200
  #define MOTHERBOARD BOARD_RAMPS_14_EFF
#define EXTRUDERS 2
#define POWER_SUPPLY 0
#define TEMP_SENSOR_0 998
#define TEMP_SENSOR_1 998
#define TEMP_SENSOR_2 0
#define TEMP_SENSOR_3 0
#define TEMP_SENSOR_4 0
#define TEMP_SENSOR_BED 0
#define DUMMY_THERMISTOR_998_VALUE 25
#define DUMMY_THERMISTOR_999_VALUE 100
#define MAX_REDUNDANT_TEMP_SENSOR_DIFF 10
#define TEMP_RESIDENCY_TIME 10  // (seconds)
#define TEMP_HYSTERESIS 3       // (degC) range of +/- temperatures considered "close" to the target one
#define TEMP_WINDOW     1       // (degC) Window around target to start the residency timer x degC early.
#define TEMP_BED_RESIDENCY_TIME 10  // (seconds)
#define TEMP_BED_HYSTERESIS 3       // (degC) range of +/- temperatures considered "close" to the target one
#define TEMP_BED_WINDOW     1       // (degC) Window around target to start the residency timer x degC early.
#define HEATER_0_MINTEMP 5
#define HEATER_1_MINTEMP 5
#define HEATER_2_MINTEMP 5
#define HEATER_3_MINTEMP 5
#define HEATER_4_MINTEMP 5
#define BED_MINTEMP 5
#define HEATER_0_MAXTEMP 275
#define HEATER_1_MAXTEMP 275
#define HEATER_2_MAXTEMP 275
#define HEATER_3_MAXTEMP 275
#define HEATER_4_MAXTEMP 275
#define BED_MAXTEMP 150
#define PIDTEMP
#define BANG_MAX 255 // limits current to nozzle while in bang-bang mode; 255=full current
#define PID_MAX BANG_MAX // limits current to nozzle while PID is active (see PID_FUNCTIONAL_RANGE below); 255=full current
  #define PID_FUNCTIONAL_RANGE 10 // If the temperature difference between the target temperature and the actual temperature
  #define K1 0.95 //smoothing factor within the PID
  #define  DEFAULT_Kp 22.2
  #define  DEFAULT_Ki 1.08
  #define  DEFAULT_Kd 114
#define MAX_BED_POWER 255 // limits duty cycle to bed; 255=full current
#define PREVENT_COLD_EXTRUSION
#define EXTRUDE_MINTEMP 170
#define PREVENT_LENGTHY_EXTRUDE
#define EXTRUDE_MAXLENGTH 200
#define THERMAL_PROTECTION_HOTENDS // Enable thermal protection for all extruders
#define THERMAL_PROTECTION_BED     // Enable thermal protection for the heated bed
#define USE_XMIN_PLUG
#define USE_YMIN_PLUG
#define USE_ZMIN_PLUG
#define USE_ZMAX_PLUG
#define ENDSTOPPULLUPS // Comment this out (using // at the start of the line) to disable the endstop pullup resistors
#define X_MIN_ENDSTOP_INVERTING true // set to true to invert the logic of the endstop.
#define Y_MIN_ENDSTOP_INVERTING true // set to true to invert the logic of the endstop.
#define Z_MIN_ENDSTOP_INVERTING true // set to true to invert the logic of the endstop.
#define X_MAX_ENDSTOP_INVERTING true // set to true to invert the logic of the endstop.
#define Y_MAX_ENDSTOP_INVERTING true // set to true to invert the logic of the endstop.
#define Z_MAX_ENDSTOP_INVERTING true // set to true to invert the logic of the endstop.
#define Z_MIN_PROBE_ENDSTOP_INVERTING false // set to true to invert the logic of the probe.
#define DEFAULT_AXIS_STEPS_PER_UNIT   { 50, 50, 50, 25 }
#define DEFAULT_MAX_FEEDRATE          {  120, 120, 25, 25 }
#define DEFAULT_MAX_ACCELERATION      { 100, 100, 50, 50 }
#define DEFAULT_ACCELERATION          10    // X, Y, Z and E acceleration for printing moves
#define DEFAULT_RETRACT_ACCELERATION  30    // E acceleration for retracts
#define DEFAULT_TRAVEL_ACCELERATION   20    // X, Y, Z acceleration for travel (non printing) moves
#define DEFAULT_XJERK                 5.0
#define DEFAULT_YJERK                 5.0
#define DEFAULT_ZJERK                  0.4
#define DEFAULT_EJERK                  5.0
#define Z_MIN_PROBE_USES_Z_MIN_ENDSTOP_PIN
#define X_PROBE_OFFSET_FROM_EXTRUDER 10  // X offset: -left  +right  [of the nozzle]
#define Y_PROBE_OFFSET_FROM_EXTRUDER 10  // Y offset: -front +behind [the nozzle]
#define Z_PROBE_OFFSET_FROM_EXTRUDER 0   // Z offset: -below +above  [the nozzle]
#define XY_PROBE_SPEED 8000
#define Z_PROBE_SPEED_FAST HOMING_FEEDRATE_Z
#define Z_PROBE_SPEED_SLOW (Z_PROBE_SPEED_FAST / 2)
#define Z_CLEARANCE_DEPLOY_PROBE   10 // Z Clearance for Deploy/Stow
#define Z_CLEARANCE_BETWEEN_PROBES  5 // Z Clearance between probe points
#define Z_PROBE_OFFSET_RANGE_MIN -20
#define Z_PROBE_OFFSET_RANGE_MAX 20
#define X_ENABLE_ON 1
#define Y_ENABLE_ON 1
#define Z_ENABLE_ON 1
#define E_ENABLE_ON 0 // For all extruders
#define DISABLE_X false
#define DISABLE_Y false
#define DISABLE_Z false
#define DISABLE_E false // For all extruders
#define DISABLE_INACTIVE_EXTRUDER true // Keep only the active extruder enabled.
#define INVERT_X_DIR false
#define INVERT_Y_DIR true
#define INVERT_Z_DIR false
#define INVERT_E0_DIR false
#define INVERT_E1_DIR false
#define INVERT_E2_DIR false
#define INVERT_E3_DIR false
#define INVERT_E4_DIR false
#define X_HOME_DIR -1
#define Y_HOME_DIR -1
#define Z_HOME_DIR 1
#define X_MIN_POS 0
#define Y_MIN_POS 0
#define Z_MIN_POS 0
#define X_MAX_POS 300
#define Y_MAX_POS 300
#define Z_MAX_POS 100
#define MANUAL_X_HOME_POS 0
#define MANUAL_Y_HOME_POS 0
#define MANUAL_Z_HOME_POS 0
#define HOMING_FEEDRATE_XY (10*60)
#define HOMING_FEEDRATE_Z  (5*60)
#define EEPROM_SETTINGS // Enable for M500 and M501 commands
#define EEPROM_CHITCHAT   // Give feedback on EEPROM commands. Disable to save PROGMEM.
#define HOST_KEEPALIVE_FEATURE        // Disable this if your host doesn't like keepalive messages
#define DEFAULT_KEEPALIVE_INTERVAL 2  // Number of seconds between "busy" messages. Set with M113.
#define PREHEAT_1_TEMP_HOTEND 180
#define PREHEAT_1_TEMP_BED     70
#define PREHEAT_1_FAN_SPEED     0 // Value from 0 to 255
#define PREHEAT_2_TEMP_HOTEND 240
#define PREHEAT_2_TEMP_BED    110
#define PREHEAT_2_FAN_SPEED     0 // Value from 0 to 255
#define PRINTJOB_TIMER_AUTOSTART
#define LCD_LANGUAGE en
#define DISPLAY_CHARSET_HD44780 JAPANESE
#define DOGLCD      // Full graphics display
#define SDSUPPORT
#define ENCODER_STEPS_PER_MENU_ITEM 2
#define REVERSE_MENU_DIRECTION
#define INDIVIDUAL_AXIS_HOMING_MENU
#define SPEAKER
#define LCD_FEEDBACK_FREQUENCY_DURATION_MS 50
#define LCD_FEEDBACK_FREQUENCY_HZ 5000
#define REPRAP_DISCOUNT_FULL_GRAPHIC_SMART_CONTROLLER
#define FAST_PWM_FAN
#define SOFT_PWM_SCALE 0
#define SERVO_DELAY 300
#define DEFAULT_NOMINAL_FILAMENT_DIA 3.00   // (mm) Diameter of the filament generally used (3.0 or 1.75mm), also used in the slicer. Used to validate sensor reading.

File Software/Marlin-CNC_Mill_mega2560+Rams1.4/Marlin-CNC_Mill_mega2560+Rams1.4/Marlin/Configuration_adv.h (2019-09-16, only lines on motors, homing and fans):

#define E0_AUTO_FAN_PIN -1
#define E1_AUTO_FAN_PIN -1
#define E2_AUTO_FAN_PIN -1
#define E3_AUTO_FAN_PIN -1
#define E4_AUTO_FAN_PIN -1
#define X_HOME_BUMP_MM 5
#define Y_HOME_BUMP_MM 5
#define Z_HOME_BUMP_MM 2
#define HOMING_BUMP_DIVISOR {2, 2, 4}  // Re-Bump Speed Divisor (Divides the Homing Feedrate)
#define MICROSTEP_MODES {16,16,16,16,16} // [1,2,4,8,16]
#define DIGIPOT_I2C_MOTOR_CURRENTS { 1.0, 1.0, 1.0, 1.0, 1.0, 1.0, 1.0, 1.0 }  //  AZTEEG_X3_PRO

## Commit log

2018-01-22 Primer commit el protocolo ya ha sido entregado en su primera version
    [Bancada eje z.SLDPRT, CNC 1.0.SLDASM, Conjunto rodillo eje Y.SLDASM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]
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2018-02-12 Diseño de la base para soporte de piezas desmontable y modelado del spindle
    [Bancada eje z.SLDPRT, Base desmontable.SLDPRT, Base.SLDASM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]
2018-02-23 Diseño de seguros para la base de maquinado
    [Seguro chino.SLDASM, Seguro de la base 1.SLDPRT]
2018-03-14 Correccion de titulos, carta de tema en protocolo y diseño de soporte de motores para el eje y
    [Conjunto rodillo eje Y.SLDASM, Eje de Rodillo en Y.SLDPRT, Seguro chino.SLDASM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]
2018-04-03 Modificacion de la base de maquinado y montaje del tornillo de bolas en el eje Z
    [4556T830_MOUNTING BRACKET.SLDPRT, Bancada eje z.SLDPRT, Base desmontable.SLDPRT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]
2018-04-10 cambio de rodamientos y fabricacion de piezas para el arnes electrico
    [Bancada eje z.SLDPRT, Base desmontable.SLDPRT, Base.SLDASM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]
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2018-10-03 Se añadieron algunas bibliografias sobre robotica ,programacion en gcode y programas cad-cam para documentar la monografia ademas se añadio el diseño original del cnc debido a que esta va a ser la ma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
    [CPJC20-RD-5-8.SLDPRT, Cabezal eje Z.SLDASM, Materia prima.SLDPRT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]
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2018-10-03 Rediseño de eje Y cambio de rodamientos y cambio de cama de maquinado.
    [CPJC20-RD-5-8.SLDPRT, Cabezal eje Z.SLDASM, Cama base maquinado.SLDPRT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]
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2018-11-06 Se quemo el bootloader del marlin para CNC en el arduino 2560
    [Configuration.h, Configuration_adv.h]
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2018-11-26 Se anexaron los diagramas de flujo para los procesos de manufactura genericos.
    [CPJC20-RD-5-8.SLDPRT, Cabezal eje Z.SLDASM, Cama base maquinado.SLDPRT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]
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2019-01-11 Modelado de piezas compradas, redisenho de ejes y ademas de cronograma de actividades para la actualizacion de la maquina
    [base soportes guias eje y derecho.SLDPRT, base soportes guias eje y izquierda.SLDPRT, cnc 4.0.SLDASM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]
2019-01-11 rediseño base carro eje y
    [CPJC20-RD-5-8.SLDPRT, arandela 8x18.SLDPRT, asiento de rodamiento.SLDPRT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]
2019-01-11 Revert "rediseño base carro eje y"
    This reverts commit f7179ad065068e427108743df24a3f0dfb6bcbb3.
    [CPJC20-RD-5-8.SLDPRT, arandela 8x18.SLDPRT, asiento de rodamiento.SLDPRT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]
2019-01-14 Se volvio a actualizar repositorio con actualizaciones al diseño que ya habian sido presentados debido a incompatibilidades entre las versiones de los archivos de las piezas del ensamble
    [CPJC20-RD-5-8.SLDPRT, arandela 8x18.SLDPRT, asiento de rodamiento.SLDPRT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]
2019-01-14 Rediseño carro eje z
    [CPJC20-RD-5-8.SLDPRT, Cabezal eje Z.SLDASM, arandela 8x18.SLDPRT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]
2019-01-15 Se agrego libreria de perfileria y planos de fabricacion de estructura eje y
    [CPJC20-RD-5-8.SLDPRT, Cabezal eje Z.SLDASM, arandela 8x18.SLDPRT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]
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2019-01-25 se agrego plano de manufactura del carro del eje z
    [CPJC20-RD-5-8.SLDPRT, Cabezal eje Z.SLDASM, Ensamblaje1.sldasm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]
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2019-01-31 Diseño de bancada eje z ,modelado de tornillo de bolas y planos para manufactura
    [CPJC20-RD-5-8.SLDPRT, Cabezal eje Z.SLDASM, Ensamblaje1.sldasm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]
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2019-02-05 acople de bancada eje Y con conjunto motriz
    [CPJC20-RD-5-8.SLDPRT, Cabezal eje Z.SLDASM, Ensamblaje1.sldasm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]
2019-02-11 Diseño de case para el conjunto motriz eje Y
    [CPJC20-RD-5-8.SLDPRT, Cabezal eje Z.SLDASM, Ensamblaje1.sldasm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]
2019-03-10 Se diseño el case para los componentes electronicos y se hicieron modificacion en el firmaware de la maquina (Marlin) para el correcto funcionamiento de los nuevos controladores de motor
    [CPJC20-RD-5-8.SLDPRT, Cabezal eje Z.SLDASM, Configuration.h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]
2019-03-22 Redaccion de carta de prorroga y adicion de fuente de poder al disenho de SW
    [Brida de arista case superior.SLDDRW, Brida de arista case superior.sldprt, CPJC20-RD-5-8.SLDPRT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]
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2019-04-16 reestructuracion diagrama de flujo de diseño en documento monografico
    [Diagrama electrico.SLDDRW]
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2019-05-15 Se añadio el subacapite de macroeconomia y se reforzaron los antecedentes ademas del informe que se hizo para los consultores para el taller de cnc que se planea instalar
    [Nicaraga 2006-2018 Sectores economicos.xls]
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2019-06-07 documentacion proceso de soldadura y diagrama de cable VGA para ejes independientes
    [Diagrama VGA.SLDDRW]
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2019-06-12 tornillos a cama de maquinado y tuerca de potencia
    [marco 4.0.SLDASM]
2019-06-13 Cajetin formato A4 y planos de soportes asociados a estructura base y eje x
    [asiento de rodamiento.SLDDRW, asiento de rodamiento.SLDPRT, base 2x1 frontal.SLDPRT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]
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2019-06-15 Plano ensable eje x y eslabon de arnes electrico
    [base eje Y rediseñado.SLDDRW, base spindle.SLDPRT, cadena.SLDASM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]
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2019-06-20 Lista de piezas clasificadas por proceso de manufactura
    [Conjunto eje Y rediseñado.SLDDRW, Copia de Estructura base eje Y.sldasm, Eje Y.xlsx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]
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2019-06-20 Tabla general de piezas y planos case electroninca.
    [Brida de arista case superior.sldprt, CPJC20-RD-5-8.SLDPRT, Cabezal eje Z.SLDASM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]
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2019-06-21 Se anexo tabla de piezas en documento acapite de manufactura
    [CPJC20-RD-5-8.SLDPRT, Cabezal eje Z.SLDASM, Case electronica.SLDDRW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]
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2019-07-02 Adicion de probe leveling al firmaware y modelos electronicos al ensamble general
    [CPJC20-RD-5-8.SLDPRT, Cabezal eje Z.SLDASM, Configuration.h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]
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2019-07-16 Diseno de camisa escalonada para tornillos de portencia y se digitalizaron las observaciones del cuabno
    [Arnes electrico eje y.SLDASM, Arnes electrico eje z.SLDASM, Asiento soporte de eje.SLDPRT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]
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2019-09-03 Reconfiguracion de inactividad en stepper electronica y patrones gcode para pruebas de fabricacion
    [Configuration.h]
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2019-09-27 Se corrigieron algunos errores de redaccion
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2019-10-02 Se anexa la tabla de gastos financieros y se actualizo el acapite de aspectos financieros
    [Gastos financieros.xlsx]
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

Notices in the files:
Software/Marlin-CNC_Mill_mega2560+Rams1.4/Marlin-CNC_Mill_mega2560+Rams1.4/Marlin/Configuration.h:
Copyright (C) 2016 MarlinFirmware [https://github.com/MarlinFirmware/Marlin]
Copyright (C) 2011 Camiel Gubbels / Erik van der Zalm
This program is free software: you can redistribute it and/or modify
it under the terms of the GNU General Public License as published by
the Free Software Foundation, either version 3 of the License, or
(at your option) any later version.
